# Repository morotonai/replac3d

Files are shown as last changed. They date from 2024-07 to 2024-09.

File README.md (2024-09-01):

# replac3d

The replac3d project is a robot that replaces the build plate of a Bambu Lab P1 and X1 series 3D printer.

I am especially proud of this project because it was is first personal technical project. I had no electronics knowledge prior, and had to learn all about stepper motors, driver boards, soldering, and code. All parts of the build are custom, and most were manufactured in-house with a CNC router!

The inspiration for this project came from my robotics competition season. I had to print many parts quickly for rapid prototyping, but couldn't remove a print after it finished due to my commitments (some of which are several hours long), wasting printing time. 

I did quite some research and noticed the following faults in existing solutions.

- I noticed most automated printing was done using the toolhead to eject the part off the bed. However, this does not work for short prints, can damage the part and toolhead, and requires catching it out of the air.
- Thomas Sanladerer's conveyor belt of build plates only works with a printer that can pass build plates through it, which does not work for the P1S (my printer) or X1C, and also involves free-fall.
- Many others I saw scraped the print off of the build plate, but this could possibly damage prints and the build plate, large prints could tip over, and small things like brims could be missed.

I was also inspired by the Prusa AFS system, but it is way too large, and grasps the build plate at the edge, which could cause prints to fall off due to the build plate bending, especially large prints that weigh it down.

Because of this, I decided to use 4 electromagnets to magnetically attract the build plate, overcoming the strength of the bed magnet.

This project is still in progress, and will be periodically updated.

Here is a YouTube link with a demo video! https://www.youtube.com/watch?v=nJoyHpohkoQ

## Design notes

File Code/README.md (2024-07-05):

# Progress

Hello,

I have made quite some progress with code and wiring of this project.

I have programmed the motors shown here:

https://cdn.discordapp.com/attachments/1082098360107941960/1258902945031000114/IMG_5098.mov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

I have tested the magnets shown here:

https://github.com/morotonai/replac3d/assets/156618723/944a391e-ea40-470c-b5c2-92e37062ae4d

The wiring is all soldered to a perfboard. A picture is attached below.



Please note that I have not thoroughly tested the magnets on the actual assembly, as I am still working the project.

I chose to use an Arduino UNO for its increased digital output performance. I found it difficult to get the same consistent performance with my Raspberry Pi 2.

I also chose to use the TMC2209 over the TMC5160 (which I tested) because of its programming simplicity - no need for SPI or serial, it is easy to pulse. This means it may be easier to integrate with nanpy later.

I plan to change the 80T extension pulleys to 20T due to torque issues and sufficient speed.

Thank you!

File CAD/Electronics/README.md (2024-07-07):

# Electronics

This folder contains the CAD files of the electronics used in this project, as well as various mounting for electrical things like drag chains.

I finished assembling it all. Videos are uploaded to this folder. Pictures are below:





## Because the files are too large, I put them into a Google Drive folder below:
https://drive.google.com/drive/folders/1wvcjFxm6h9ep14Qb6PPWo3LjFd0fDXGs?usp=sharing

## Drag Chain


## Control


## 5V Power


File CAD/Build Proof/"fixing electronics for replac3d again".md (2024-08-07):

found m2 allen wrench


detached raspberry pi


removed perfboard screw and cleared area between the step dir pins where i thought it was bridging


vibration problem is likely due to current imbalance between motors, because step and dir pins are not bridged

https://github.com/user-attachments/assets/8728fe7b-3f46-40bb-9ebd-699f81843bba

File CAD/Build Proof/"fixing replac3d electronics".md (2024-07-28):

unscrewed arduino screws



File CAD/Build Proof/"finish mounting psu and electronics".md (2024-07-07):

mounted psu on one side, had to use m3 screw because of CAD inaccuracy

also ziptied the stepper motor cables into a loop



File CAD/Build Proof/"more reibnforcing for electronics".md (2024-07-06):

extruded reinforcements and reinforced perfboard mounting





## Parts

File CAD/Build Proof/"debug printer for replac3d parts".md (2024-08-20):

printer nozzle clogged


extruder disassembled but was nozzle thats clogged


replacing nozzle


and finished


back to printing


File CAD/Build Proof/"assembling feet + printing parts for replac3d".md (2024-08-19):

assembling feet






slicing


started print



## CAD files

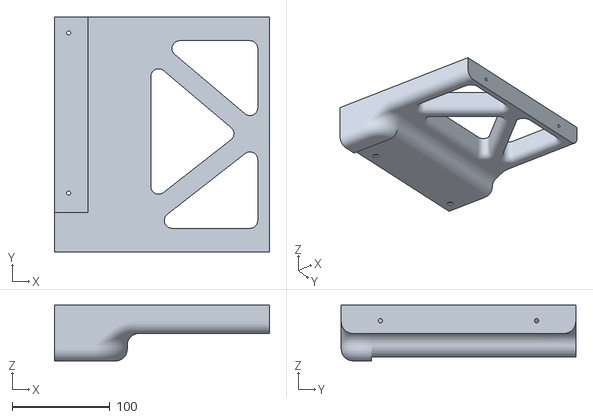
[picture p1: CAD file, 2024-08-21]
CAD/Electronics/Plate Holder Mirror 1.stl
220.0 x 240.0 x 57.1

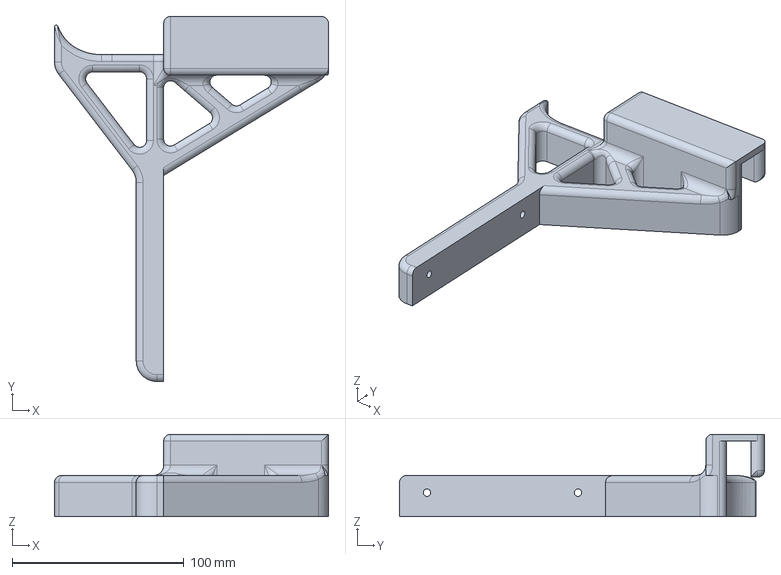
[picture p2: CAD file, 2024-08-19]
CAD/Extending Assembly/Printer Brace 08192024.step
159.6 x 212.6 x 48.0 mm

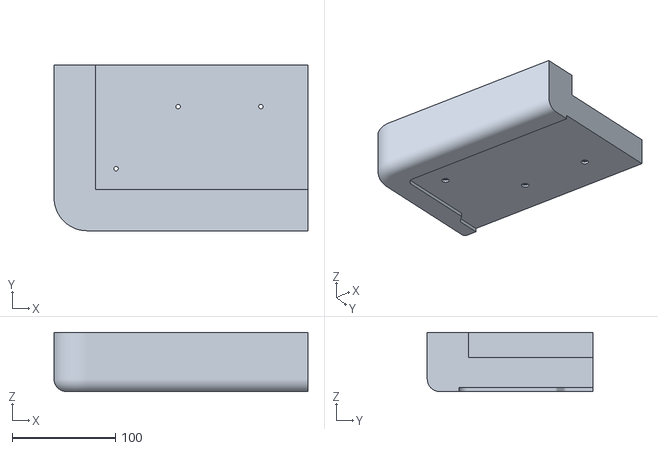
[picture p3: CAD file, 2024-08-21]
CAD/Electronics/Plate Holder Mirror 2.stl
245.5 x 160.0 x 57.1

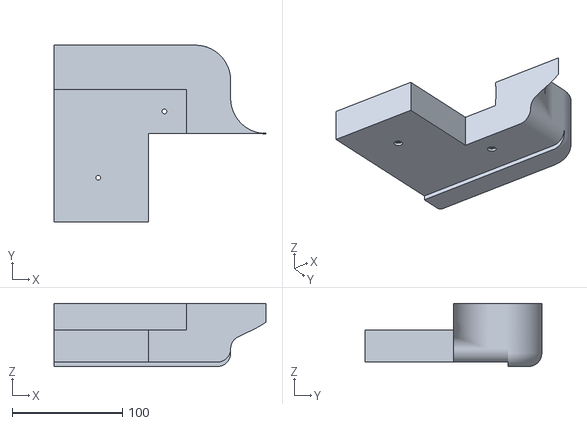
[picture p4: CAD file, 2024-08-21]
CAD/Electronics/Plate Holder Mirror 3.stl
192.0 x 160.0 x 57.1

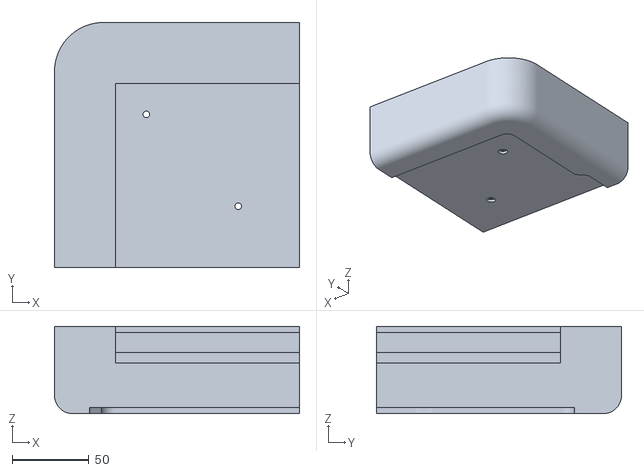
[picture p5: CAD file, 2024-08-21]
CAD/Electronics/Plate Holder Mirror 4.stl
160.0 x 160.0 x 57.1

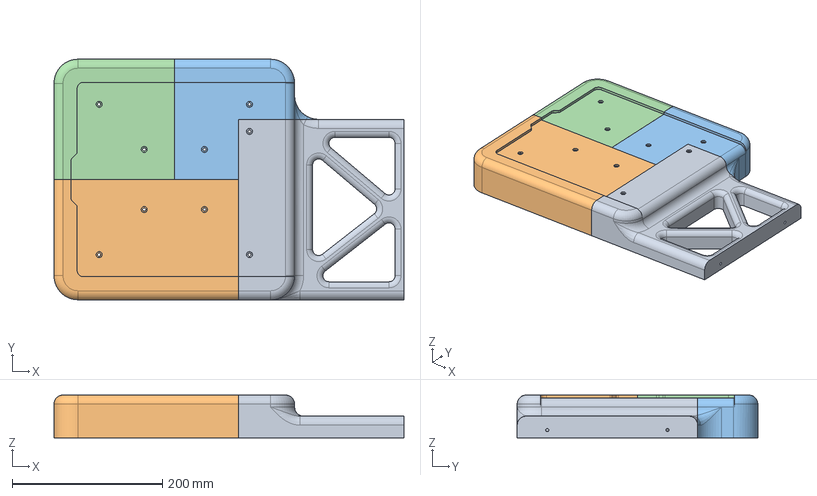
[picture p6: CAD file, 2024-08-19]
CAD/Electronics/Plate Holder 08192024.step
465.5 x 320.0 x 57.1 mm

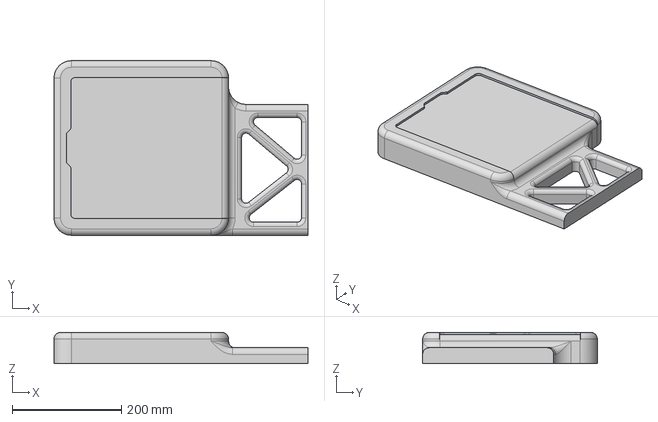
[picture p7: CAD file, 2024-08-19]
CAD/Electronics/Plate Holder v1.step
465.5 x 320.0 x 57.1 mm

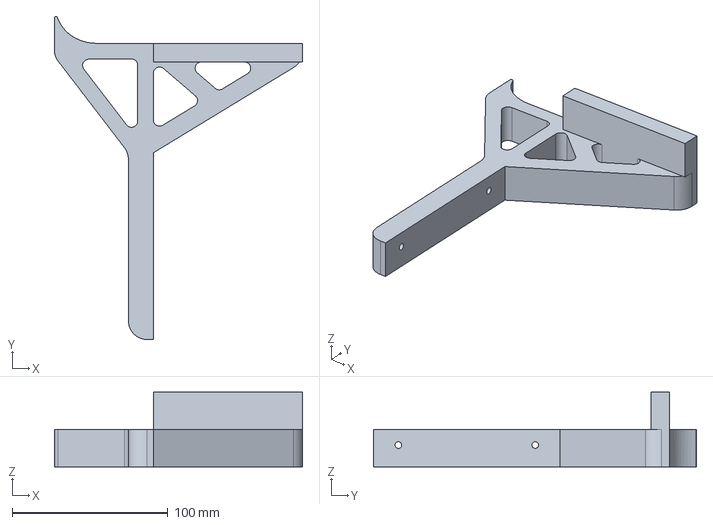
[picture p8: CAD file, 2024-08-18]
CAD/Electronics/Printer Brace unfinished.step
159.6 x 207.7 x 48.0 mm

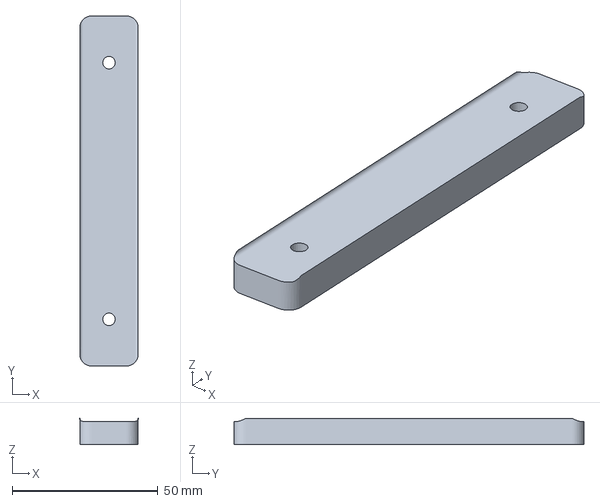
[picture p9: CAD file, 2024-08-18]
CAD/Electronics/8mm TPU Foot BambuStudio.3mf
20.0 x 120.0 x 9.00 mm

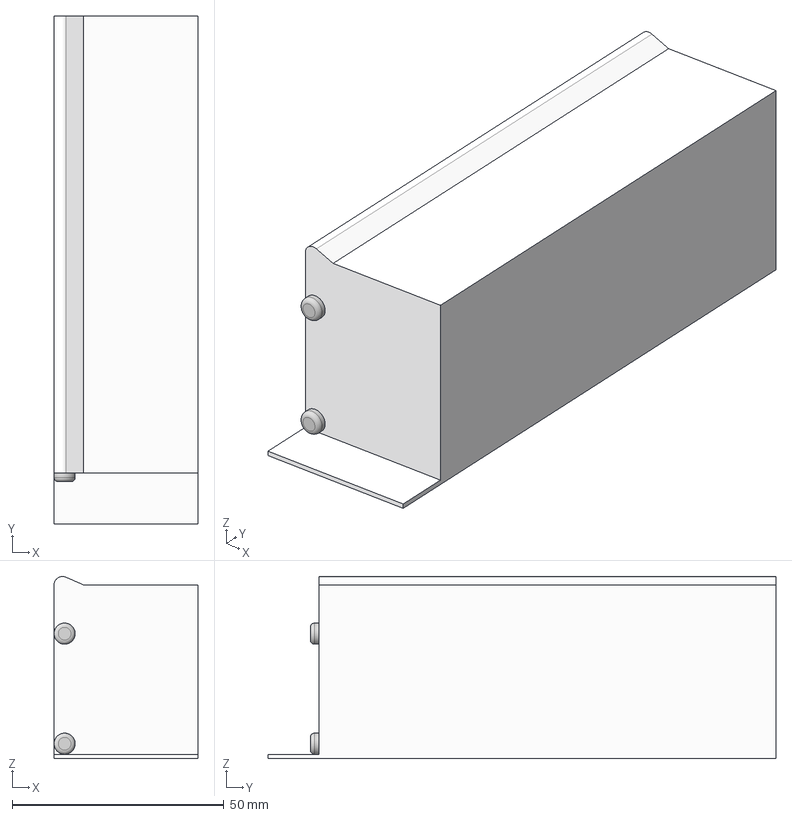
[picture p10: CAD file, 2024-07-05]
CAD/Electronics/250W 24v PSU LED Driver 10.4A v1.step
34.0 x 120.0 x 43.0 mm

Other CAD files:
CAD/Electronics/8mm TPU Foot.step
CAD/Electronics/Plate Holder 08192024.stl
CAD/Electronics/Plate Holder v1.stl
CAD/Electronics/Printer Brace unfinished.stl
CAD/Extending Assembly/Printer Brace 08192024.3mf

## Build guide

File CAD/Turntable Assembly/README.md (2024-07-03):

# Turntable Assembly

This assembly contains the structure for rotating the extending assembly for the replac3d project.

The turntable assembly uses one NEMA23 Stepper Motor and a GT2 timing belt to rotate the sliding assembly. The robot will be able to reach into the printer and extract the build plate, then turn right to deposit it, and turn left to pick up a new one to put into the printer.

## Changelog

- V29

The turntable assembly is complete with structure and power transmission.

<br>

## Updates

Printed the pulley, received the custom steel plates that I ordered, and finished assembling the whole thing.

I had to add 3D printed spacers on each of the turntable's bearing stacks, as there was not enough clearance for the screwheads.

I also added the covers on both sides for the thrust bearings (previously only one side), as the balls binded to the middle bearing and didn't spin.

https://github.com/morotonai/replac3d/assets/156618723/f7f1f9a5-5898-47ce-b88c-4b0123e87160

<br>

Below are some screenshots of the current design. For more information on the project, please read the project's README found [here](https://github.com/morotonai/replac3d/tree/main).

Thanks for your interest! Please do not hesitate to contact me with any questions on discord [here](https://discord.com/users/morotonai.3/).






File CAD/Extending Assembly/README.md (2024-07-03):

# Extending Assembly

This assembly contains the structure for extension and retraction for the replac3d project.

The extending assembly uses two NEMA17 Stepper Motors and GT2 timing belts two extend and retract four electromagnets. When energized, the electromagnets will attract to the build plate of the 3D printer. The motors will spin in opposite directions to extend and retract.

## Changelog

- V25

The motors do not include the belts, and there is no guarantee it will work in its current configuration.

- V51

The assembly is complete with belt clamps and a working (in CAD) path for the belt.

<br>

## Updates

Finished building the extending assembly (excluding bottom plate). 


Manufactured the plates using a friend's CNC router.


<br>

Below are some screenshots of the current design. For more information on the project, please read the project's README found [here](https://github.com/morotonai/replac3d/tree/main).

Thanks for your interest! Please do not hesitate to contact me with any questions on discord [here](https://discord.com/users/morotonai.3/).







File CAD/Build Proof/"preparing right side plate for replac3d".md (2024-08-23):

added tape


fits in printer and on right holder



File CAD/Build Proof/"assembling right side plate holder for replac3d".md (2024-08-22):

finished printing all  5 pieces, screwed it all together and attached to main body's extrusions





probably finished hardware:



rearranged workspace


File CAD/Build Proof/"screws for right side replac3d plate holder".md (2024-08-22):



positioned the pieces, waiting for one more print


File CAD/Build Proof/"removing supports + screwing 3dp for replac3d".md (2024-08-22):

mocked up parts that finished printing


screwed in right side mount


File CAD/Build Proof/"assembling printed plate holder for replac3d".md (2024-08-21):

new plate finished printing


screwed in all 9 screws - no wrench so had to use pliers, was very time consuming to line up the pieces as well


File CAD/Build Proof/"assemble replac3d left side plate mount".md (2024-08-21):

removed supports


moved printer onto table


positioned pieces correctly


screwed in printer prace to extrusion


plate mount screwed in as well


printing new piece


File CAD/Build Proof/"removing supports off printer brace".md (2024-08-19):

removed supports and mocked up




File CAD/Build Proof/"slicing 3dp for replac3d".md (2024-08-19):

was too large to print, resized piece to be 220mmx240mm




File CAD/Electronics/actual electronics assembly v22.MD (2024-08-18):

https://hackclub.slack.com/archives/C06SBHMQU8G/p1724001867617379?thread_ts=1723997895.926659&cid=C06SBHMQU8G



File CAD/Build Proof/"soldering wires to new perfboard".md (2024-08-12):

soldered driver


stripped wires


soldered stepper wires




found resistors, measured cut and stripped wires



soldered dir wire and added connector


soldered step wire and pull down resistor for dir



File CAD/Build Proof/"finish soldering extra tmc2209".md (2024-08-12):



soldered pull up resistor to en, pull down resistor to dir







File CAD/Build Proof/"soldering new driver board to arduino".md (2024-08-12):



removed arduino female headers


trying to solder enable pin, solder got onto other pins




3rd driver vm gnd added



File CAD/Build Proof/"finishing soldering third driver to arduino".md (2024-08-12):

soldered magnet wire



need to feed 4 new stepper wires through this...


measured and cut wires


fed through first (black) wire


fed through second (red) wire


feeding blue wire in


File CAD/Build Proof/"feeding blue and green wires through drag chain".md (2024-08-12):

fed through the blue wire


starting to feed through green wire, it is super difficult


more progress re green wire




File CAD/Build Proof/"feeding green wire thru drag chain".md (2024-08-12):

decided to keep green wire outside of drag chain for last bit, it was too hard - drag chain was completely full of wires.



doing stepper motor connections


connected left stepper motor


connected both extension stepper motors


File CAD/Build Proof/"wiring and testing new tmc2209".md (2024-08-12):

ready to test


fixed drag chain



fixed mosfet connections, wires were desoldered


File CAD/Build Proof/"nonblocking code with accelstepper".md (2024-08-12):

decided to fix nonblocking code problems with electronics only

wiring directly to other motors signal pins



screwed in arduino, need to reverse left motor poles



reversed motor polarity



testing both motors (it works) but video is too big

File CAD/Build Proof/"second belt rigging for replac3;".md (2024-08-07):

put on pulley


routed belt


tensioned belt


fixed/tightened belt


trimmed belt


testing link below (video too big for github)

still has some hiccups

https://hackclub.slack.com/archives/C06SBHMQU8G/p1722289120189139?thread_ts=1722285413.135109&cid=C06SBHMQU8G




















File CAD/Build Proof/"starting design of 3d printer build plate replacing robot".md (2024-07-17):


modeling build plate
finished modeling build plate, now modeling electromagnets



finished modeling electromagnet



modeled electromagnet placement



finished placement



created mounting plate



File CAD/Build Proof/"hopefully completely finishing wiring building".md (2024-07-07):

attached screw terminal distribution block and ziptied PSU and buck converter cables into a loop, finishing it



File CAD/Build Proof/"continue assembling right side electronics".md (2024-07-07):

screwed in mosfets and buck converter to the nuts i embedded in the back sides



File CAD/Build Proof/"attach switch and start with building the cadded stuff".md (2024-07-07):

ziptied a power switch onto the psu



finished printing right side mount and pressfit m3 nuts


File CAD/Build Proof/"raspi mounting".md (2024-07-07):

mounted raspi



and also mounted psu from one side



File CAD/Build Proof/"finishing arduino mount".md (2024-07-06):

reincforced the perfboard to the arduino, added lightening pockets



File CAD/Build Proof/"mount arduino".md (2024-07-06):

more fillets for reinforcement around the raspi mounting holes



finished the arduino mounting sketch and mounted the arduino (extruded offset holes and cut down size of mounting board)



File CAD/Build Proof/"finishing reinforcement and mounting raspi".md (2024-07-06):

filleted inner and outer edges



added hex nut cutouts for raspi 


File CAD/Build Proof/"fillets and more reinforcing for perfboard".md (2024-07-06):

filleted the reinforcements for perfboard and psu

adding further reinforcement to perfboard mounting including pockets (kinda hard to see, but theres an additional beam supporting the perfboard connecting it with the big psu triangle)



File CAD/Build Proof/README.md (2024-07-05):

This contains all the build proof for HCA.

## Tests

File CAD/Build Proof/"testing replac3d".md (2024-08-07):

https://github.com/user-attachments/assets/50033d5d-a1b8-41a6-b5be-362c742bdce0
set up replac3d with printer


tuned to drop off the build plate, but the stepper motors are not strong enough to pull the plate out.

https://github.com/user-attachments/assets/5fb26e7f-c739-4e24-adc0-14c6cf66a74d

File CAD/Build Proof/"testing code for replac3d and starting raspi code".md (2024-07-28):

attached belt




figured out that step and dir pins are bridging somewhere


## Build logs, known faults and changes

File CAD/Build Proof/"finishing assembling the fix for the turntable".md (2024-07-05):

testing spinning, it spins smoothly, tightened all the screws



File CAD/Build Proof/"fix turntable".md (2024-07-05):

attached the standoffs with the spacer with different screws


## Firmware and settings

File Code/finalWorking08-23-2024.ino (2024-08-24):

#include <AccelStepper.h>

#define pul1 3
#define dir1 2

#define pul2 5
#define dir2 4

#define en1 6
#define en2 7
#define en3 11

#define magnet 10

AccelStepper extension(1, pul1, dir1);
AccelStepper panning(1, pul2, dir2);

void setParams(){
  pinMode(en1, OUTPUT);
  pinMode(en2, OUTPUT);
  pinMode(en3, OUTPUT);

  pinMode(magnet, OUTPUT);

  extension.setMaxSpeed(3000);
  extension.setAcceleration(1000);

  panning.setMaxSpeed(1000);
  panning.setAcceleration(1000);
}

void panTo(const String& direction) {
  digitalWrite(en1, LOW);
    if (direction == "left") {
        panning.runToNewPosition(-1450);
    } else if (direction == "middle") {
        panning.runToNewPosition(0);
    } else if (direction == "right") {
        panning.runToNewPosition(1440);
    }
}

void extendTo(const String& position) {
    digitalWrite(en2, LOW);
    digitalWrite(en3, LOW);
    if (position == "in") {
        extension.runToNewPosition(0);
    } else if (position == "out") {
        extension.runToNewPosition(-14000);
    }
}

void retrieve(){
  digitalWrite(magnet, LOW);
  extendTo("in");
  panTo("middle");
  extendTo("out");
  delay(500);
  digitalWrite(magnet, HIGH);
  delay(500);
  extendTo("in");
}

void deposit(){
  digitalWrite(magnet, HIGH);
  extendTo("in");
  panTo("right");
  extendTo("out");
  delay(500);
  digitalWrite(magnet, LOW);
  delay(500);
  extendTo("in");
}

void pickup(){
  digitalWrite(magnet, LOW);
  extendTo("in");
  panTo("left");
  extendTo("out");
  delay(500);
  digitalWrite(magnet, HIGH);
  delay(500);
  extendTo("in");
}

void replace(){
  digitalWrite(magnet, HIGH);
  extendTo("in");
  panTo("middle");
  extendTo("out");
  delay(500);
  digitalWrite(magnet, LOW);
  delay(500);
  extendTo("in");
}
void setup() {
  // put your setup code here, to run once:
  setParams();

  retrieve();

  //only retrieve for now to test if steppers are strong enough to pull the build plate out of the printer
  deposit();
  pickup();
  replace(); 
}


void loop() {
  // put your main code here, to run repeatedly:
}

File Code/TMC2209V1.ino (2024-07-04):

// For arduino uno and TMC2209 stepper motor driver
// This is my initial test to make it spin

#define EN_PIN           2      // Enable - PURPLE
#define DIR_PIN1          3      // Direction - WHITE
#define STEP_PIN1         4      // Step - ORANGE
#define DIR_PIN2         5
#define STEP_PIN2          6      // Software Slave Clock (SCK) - GREEN

int target1;
int target2;
int delay1;
int delay2;
bool dir = false;
bool codeExecuted = false;

//== Setup ===============================================================================

void setup() {
  pinMode(EN_PIN, OUTPUT);           // Set pinmodes
  pinMode(STEP_PIN1, OUTPUT);
  pinMode(DIR_PIN1, OUTPUT);
  pinMode(STEP_PIN2, OUTPUT);
  pinMode(DIR_PIN2, OUTPUT);
  digitalWrite(EN_PIN, HIGH);       
}

//== Loop =================================================================================

void loop() {

  if (!codeExecuted){
      target1 = 1600;
      target2 = 3200;
      delay1 = 2500;
      delay2 = 300;
  digitalWrite(DIR_PIN1, LOW);
    for (int i = 0; i <= target1; i++){     
      digitalWrite(EN_PIN, LOW);      didn       
    digitalWrite(STEP_PIN1, HIGH);
    delayMicroseconds(delay1);
    
    digitalWrite(STEP_PIN1, LOW);
        delayMicroseconds(delay1);

    //delay(2000);
  }
      digitalWrite(DIR_PIN2, LOW);
    for (int i = 0; i <= target2; i++){     
      digitalWrite(EN_PIN, LOW);             
    digitalWrite(STEP_PIN2, HIGH);
    delayMicroseconds(delay2);
    
    digitalWrite(STEP_PIN2, LOW);
        delayMicroseconds(delay2);

    //delay(2000);
  }
      digitalWrite(DIR_PIN2, HIGH);
    for (int i = 0; i <= target2; i++){     
      digitalWrite(EN_PIN, LOW);             
    digitalWrite(STEP_PIN2, HIGH);
    delayMicroseconds(delay2);
    
    digitalWrite(STEP_PIN2, LOW);
        delayMicroseconds(delay2);

    //delay(2000);
  }
  digitalWrite(DIR_PIN1, HIGH);

     for (int i = 0; i <= 2*target1; i++){
           
      digitalWrite(EN_PIN, LOW);             
    digitalWrite(STEP_PIN1, HIGH);
    delayMicroseconds(delay1);
    
    digitalWrite(STEP_PIN1, LOW);
        delayMicroseconds(delay1);

    //delay(2000);
  }
      digitalWrite(DIR_PIN2, LOW);
    for (int i = 0; i <= target2; i++){     
      digitalWrite(EN_PIN, LOW);             
    digitalWrite(STEP_PIN2, HIGH);
    delayMicroseconds(delay2);
    
    digitalWrite(STEP_PIN2, LOW);
        delayMicroseconds(delay2);

    //delay(2000);
  }
      digitalWrite(DIR_PIN2, HIGH);
    for (int i = 0; i <= target2; i++){     
      digitalWrite(EN_PIN, LOW);             
    digitalWrite(STEP_PIN2, HIGH);
    delayMicroseconds(delay2);
    
    digitalWrite(STEP_PIN2, LOW);
        delayMicroseconds(delay2);

    //delay(2000);
  }
    digitalWrite(DIR_PIN1, LOW);
    for (int i = 0; i <= target1; i++){     
      digitalWrite(EN_PIN, LOW);             
    digitalWrite(STEP_PIN1, HIGH);
    delayMicroseconds(delay1);
    
    digitalWrite(STEP_PIN1, LOW);
        delayMicroseconds(delay1);

    //delay(2000);
  }
    digitalWrite(DIR_PIN2, LOW);
    for (int i = 0; i <= target2; i++){     
      digitalWrite(EN_PIN, LOW);             
    digitalWrite(STEP_PIN2, HIGH);
    delayMicroseconds(delay2);
    
    digitalWrite(STEP_PIN2, LOW);
    delayMicroseconds(delay2);

    //delay(2000);
  }

    digitalWrite(DIR_PIN2, HIGH);
    for (int i = 0; i <= target2; i++){     
      digitalWrite(EN_PIN, LOW);             
    digitalWrite(STEP_PIN2, HIGH);
    delayMicroseconds(delay2);
    
    digitalWrite(STEP_PIN2, LOW);
    delayMicroseconds(delay2);

    //delay(2000);
  }  
  }
  codeExecuted = true;
}

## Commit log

2024-06-27 Added f3z and step files for sliding assembly
    Finished unpowered sliding assembly, including motors mounted, belt clamps, and all structure
2024-06-27 Updated Extending Assembly README
2024-06-28 Updated Extending Assembly README.md
2024-06-28 Added belt rigging for sliding assembly
2024-06-28 Added turntable assembly files
2024-07-03 Added Extending Assembly Updates to README
2024-07-03 Added Turntable Assembly Update to README
2024-07-04 Upload first TMC2209 Arduino Program
2024-07-04 Create AccelStepperTest.ino
    Replaces TMC2209V1 - no longer uses manual wait time, but instead uses AccelStepper library for acceleration
    [AccelStepperTest.ino]
2024-07-05 added psu (unfinished)
    [250W 24v PSU LED Driver 10.4A v1.step]
2024-07-05 Create "assembling bottom bearing assembly of turntable".md
2024-07-05 Create "more belts".md
2024-07-05 Create "rebuild stationary assembly".md
2024-07-05 Create "printing turntable pulley".md
2024-07-05 Create "build motor assembly".md
2024-07-05 Create "attaching pulley to bottom plate".md
2024-07-05 Create "more assembly for fixed turntable".md
2024-07-05 Create "start assembling turntable".md
2024-07-05 Create "belts!! for turntable and extension".md
2024-07-05 Create "finishing assembling the fix for the turntable".md
2024-07-05 Create "assembling turntable bearings".md
2024-07-05 Create "bottom plate assembly".md
2024-07-05 Create "finishing extending assemblh".md
2024-07-05 Create "attaching drag chain to motor cage".md
2024-07-05 Create "route wires through drag chain".md
2024-07-05 Create "routing more wires through drag chain".md
2024-07-06 Create "finishing drag chain wiring, maybe starting on layout".md
2024-07-06 Create "ziptying connections and tensioning belt".md
2024-07-06 Create "electronics mounting".md
2024-07-06 Create "design wiring assembly".md
2024-07-06 Create "mounting electronics".md
2024-07-06 Create "details for electronics mount".md
2024-07-06 Create "finishing reinforcement and mounting raspi".md
2024-07-06 Create "mount arduino".md
2024-07-06 Create "finishing arduino mount".md
2024-07-07 Update README.md with finished electrical CAD
2024-07-07 Create "raspi mounting".md
2024-07-07 Create "finish mounting psu and electronics".md
2024-07-07 Create "attach switch and start with building the cadded stuff".md
2024-07-07 Create "continue assembling right side electronics".md
2024-07-07 Create "hopefully completely finishing wiring building".md
2024-07-17 Create "starting design of 3d printer build plate replacing robot".md
2024-07-24 Create "wiring electromagnets for replac3d".md
2024-07-24 Create "finish soldering mosfet stuff".md
2024-08-07 Create "second belt rigging for replac3;".md
2024-08-12 Create "wiring and testing new tmc2209".md
2024-08-12 Create "feeding green wire thru drag chain".md
2024-08-12 Create "feeding blue and green wires through drag chain".md
2024-08-12 Create "finishing soldering third driver to arduino".md
2024-08-12 Create "soldering new driver board to arduino".md
2024-08-12 Create "finish soldering extra tmc2209".md
2024-08-12 Create "soldering wires to new perfboard".md
2024-08-18 Create "wiring button for replac3d".md
2024-08-18 Create actual electronics assembly v22.MD
2024-08-19 Create "removing supports off printer brace".md
2024-08-19 Create "assembling feet + printing parts for replac3d".md
2024-08-19 Add files via upload (need to reprint)
    [Printer Brace 08192024.3mf, Printer Brace 08192024.step]
2024-08-20 Create "debug printer for replac3d parts".md
2024-08-21 Create "assemble replac3d left side plate mount".md
2024-08-21 Create "assembling printed plate holder for replac3d".md
2024-08-22 Create "removing supports + screwing 3dp for replac3d".md
2024-08-22 Create "screws for right side replac3d plate holder".md
2024-08-22 Create "assembling right side plate holder for replac3d".md
2024-08-23 Create "preparing right side plate for replac3d".md
